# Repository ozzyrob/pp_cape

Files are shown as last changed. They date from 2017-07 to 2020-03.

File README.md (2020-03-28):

# pp_cape

Beaglebone Black cape to breakout signals to a 26 pin header

Intent is to replicate order of Parallel Port (not function)
to facilitate migration from x86 Linuxcnc users to BBB Machinekit
users

  * Port 1 header has 8 Outputs + 5 Inputs + 4 Outputs
  * Port 2 header has 8 Inputs + 5 Inputs + 4 Outputs
  * Pin 26 on each header is an "enable pin"
  * I2C is broken out to a 1x4 pin header (SCL SDL 3v3 DGND)
  * P9.1 to P9.10 are broken out to a 2x4 pin header
  * ADC Inputs and ADC ground are broken out (reference has not been)

To be used in conjunction with pp_bob_output & pp_bob_input boards

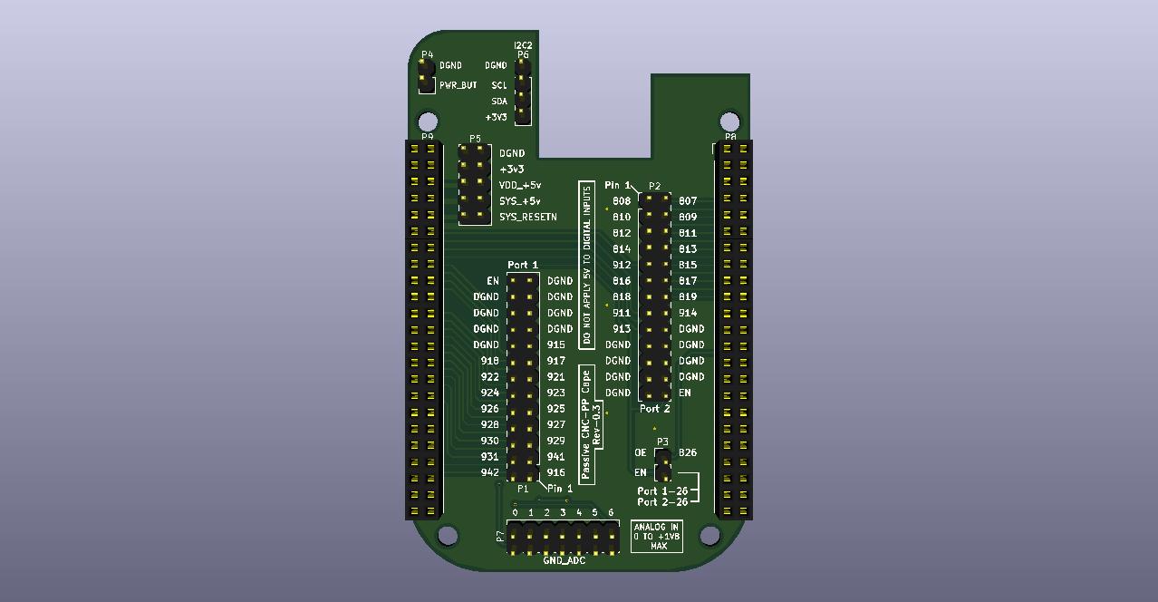
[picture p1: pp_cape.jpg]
cape


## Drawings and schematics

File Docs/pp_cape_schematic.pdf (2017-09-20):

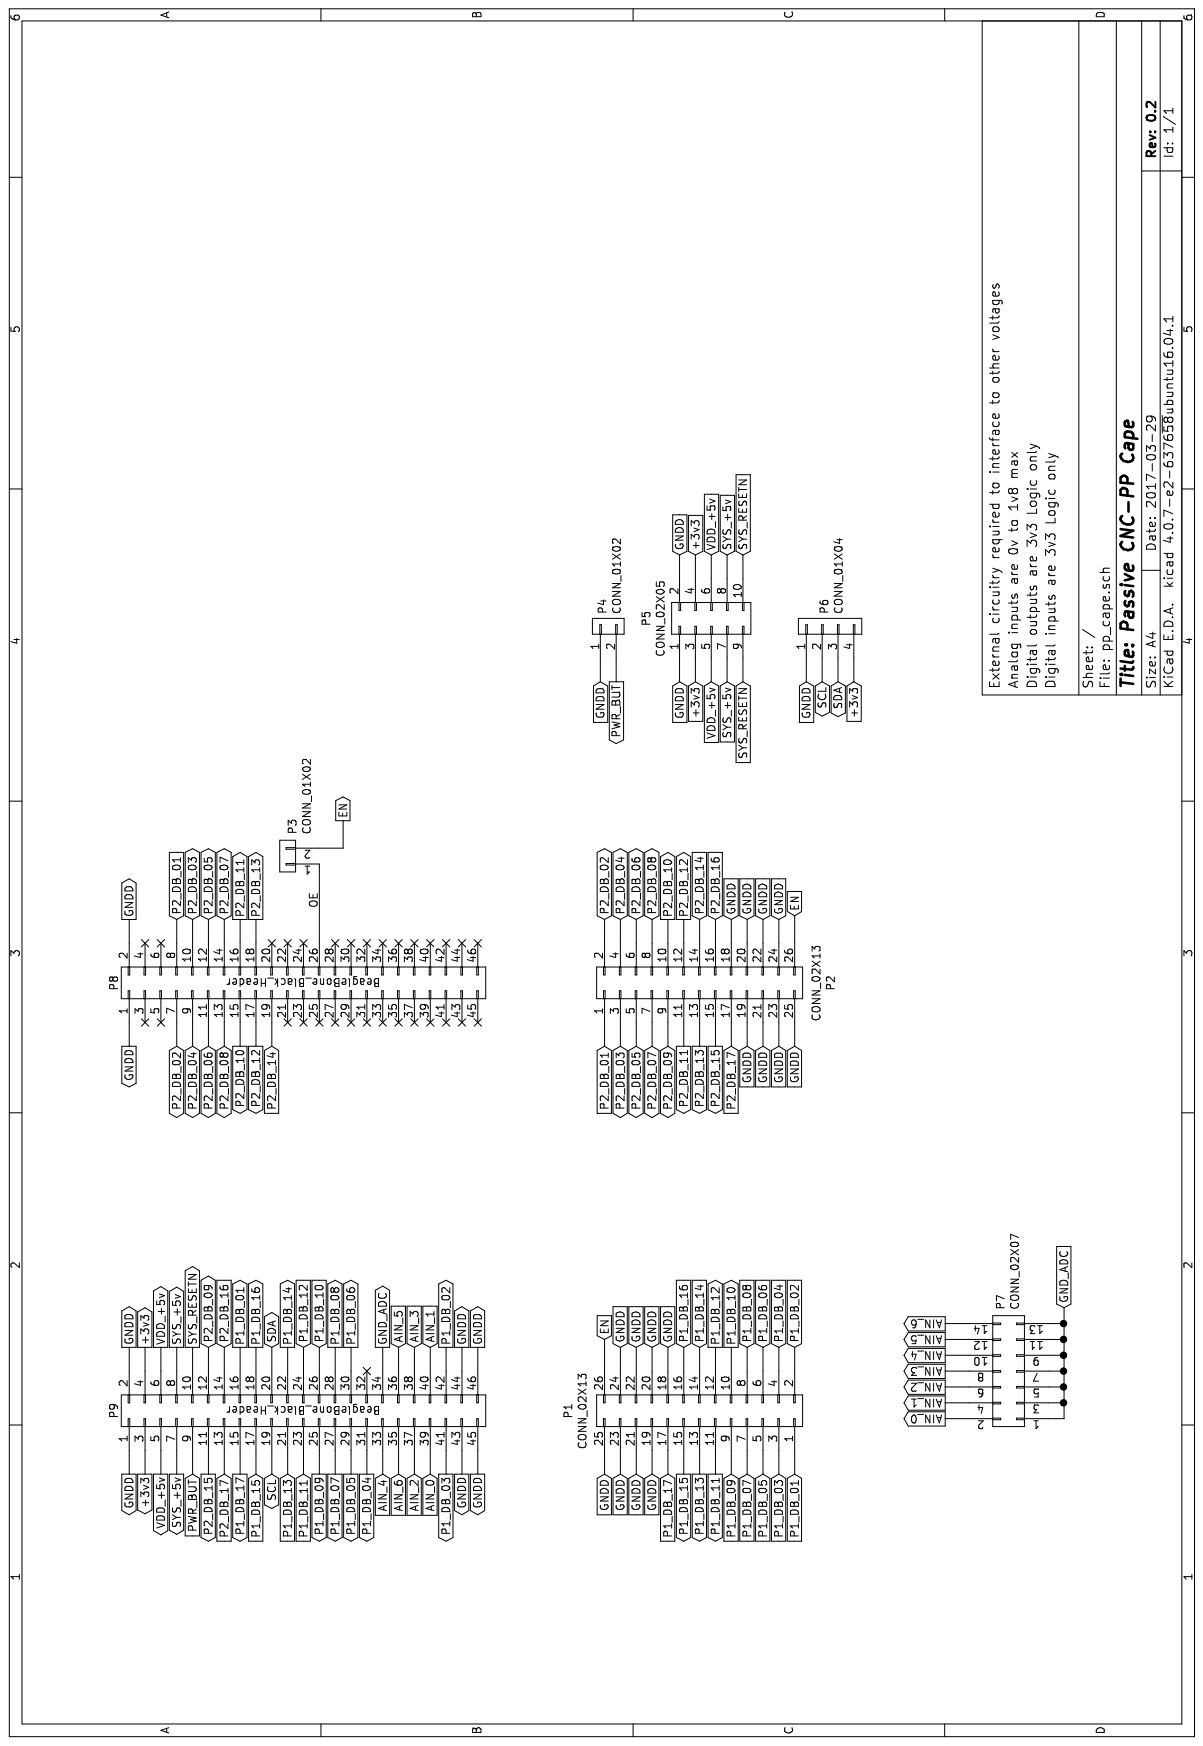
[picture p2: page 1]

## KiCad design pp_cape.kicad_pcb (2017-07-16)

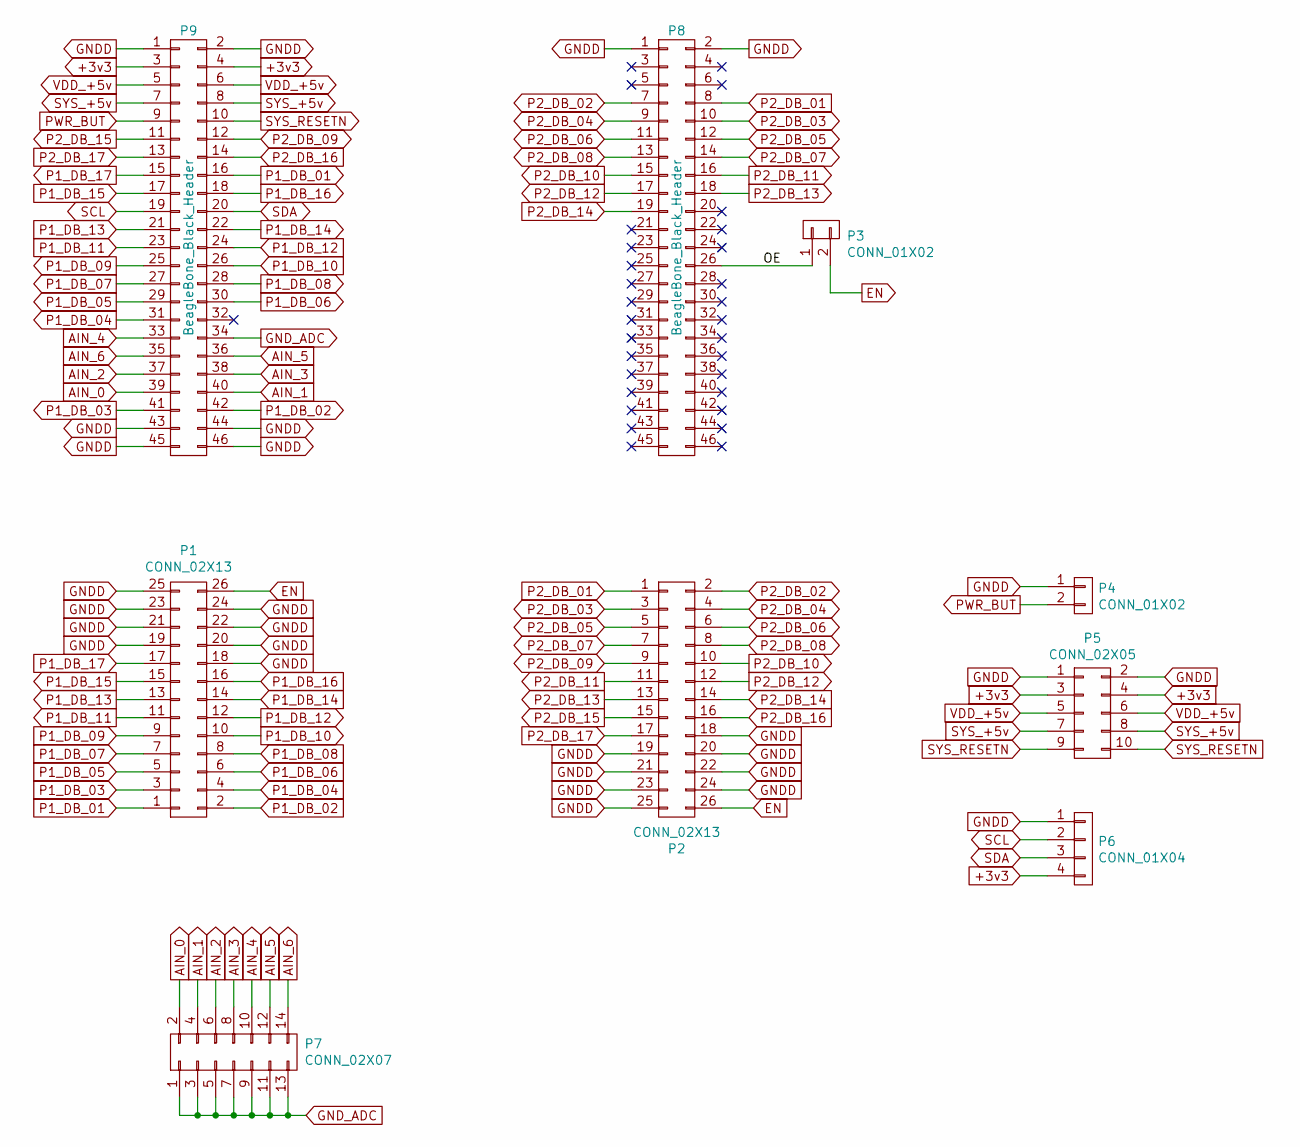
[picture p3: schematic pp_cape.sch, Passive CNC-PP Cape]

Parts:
P1, P2: CONN_02X13; Pin_Header_Straight_2x13_Pitch2.54mm
P3, P4: CONN_01X02; Pin_Header_Straight_1x02_Pitch2.54mm
P5: CONN_02X05; Pin_Header_Straight_2x05_Pitch2.54mm
P6: CONN_01X04; Pin_Header_Straight_1x04_Pitch2.54mm
P7: CONN_02X07; Pin_Header_Straight_2x07_Pitch2.54mm
P8, P9: BeagleBone_Black_Header; Socket_BeagleBone_Black

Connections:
+3v3: P5.3, P5.4, P6.4, P9.3, P9.4
/OE: P3.1, P8.26
AIN_0: P7.2, P9.39
AIN_1: P7.4, P9.40
AIN_2: P7.6, P9.37
AIN_3: P7.8, P9.38
AIN_4: P7.10, P9.33
AIN_5: P7.12, P9.36
AIN_6: P7.14, P9.35
EN: P1.26, P2.26, P3.2
GNDD: P1.18, P1.19, P1.20, P1.21, P1.22, P1.23, P1.24, P1.25, P2.18, P2.19, P2.20, P2.21, P2.22, P2.23, P2.24, P2.25, P4.1, P5.1, P5.2, P6.1, P8.1, P8.2, P9.1, P9.2, P9.43, P9.44, P9.45, P9.46
GND_ADC: P7.1, P7.3, P7.5, P7.7, P7.9, P7.11, P7.13, P9.34
P1_DB_01: P1.1, P9.16
P1_DB_02: P1.2, P9.42
P1_DB_03: P1.3, P9.41
P1_DB_04: P1.4, P9.31
P1_DB_05: P1.5, P9.29
P1_DB_06: P1.6, P9.30
P1_DB_07: P1.7, P9.27
P1_DB_08: P1.8, P9.28
P1_DB_09: P1.9, P9.25
P1_DB_10: P1.10, P9.26
P1_DB_11: P1.11, P9.23
P1_DB_12: P1.12, P9.24
P1_DB_13: P1.13, P9.21
P1_DB_14: P1.14, P9.22
P1_DB_15: P1.15, P9.17
P1_DB_16: P1.16, P9.18
P1_DB_17: P1.17, P9.15
P2_DB_01: P2.1, P8.8
P2_DB_02: P2.2, P8.7
P2_DB_03: P2.3, P8.10
P2_DB_04: P2.4, P8.9
P2_DB_05: P2.5, P8.12
P2_DB_06: P2.6, P8.11
P2_DB_07: P2.7, P8.14
P2_DB_08: P2.8, P8.13
P2_DB_09: P2.9, P9.12
P2_DB_10: P2.10, P8.15
P2_DB_11: P2.11, P8.16
P2_DB_12: P2.12, P8.17
P2_DB_13: P2.13, P8.18
P2_DB_14: P2.14, P8.19
P2_DB_15: P2.15, P9.11
P2_DB_16: P2.16, P9.14
P2_DB_17: P2.17, P9.13
PWR_BUT: P4.2, P9.9
SYS_+5v: P5.7, P5.8, P9.7, P9.8
SYS_RESETN: P5.9, P5.10, P9.10
VDD_+5v: P5.5, P5.6, P9.5, P9.6

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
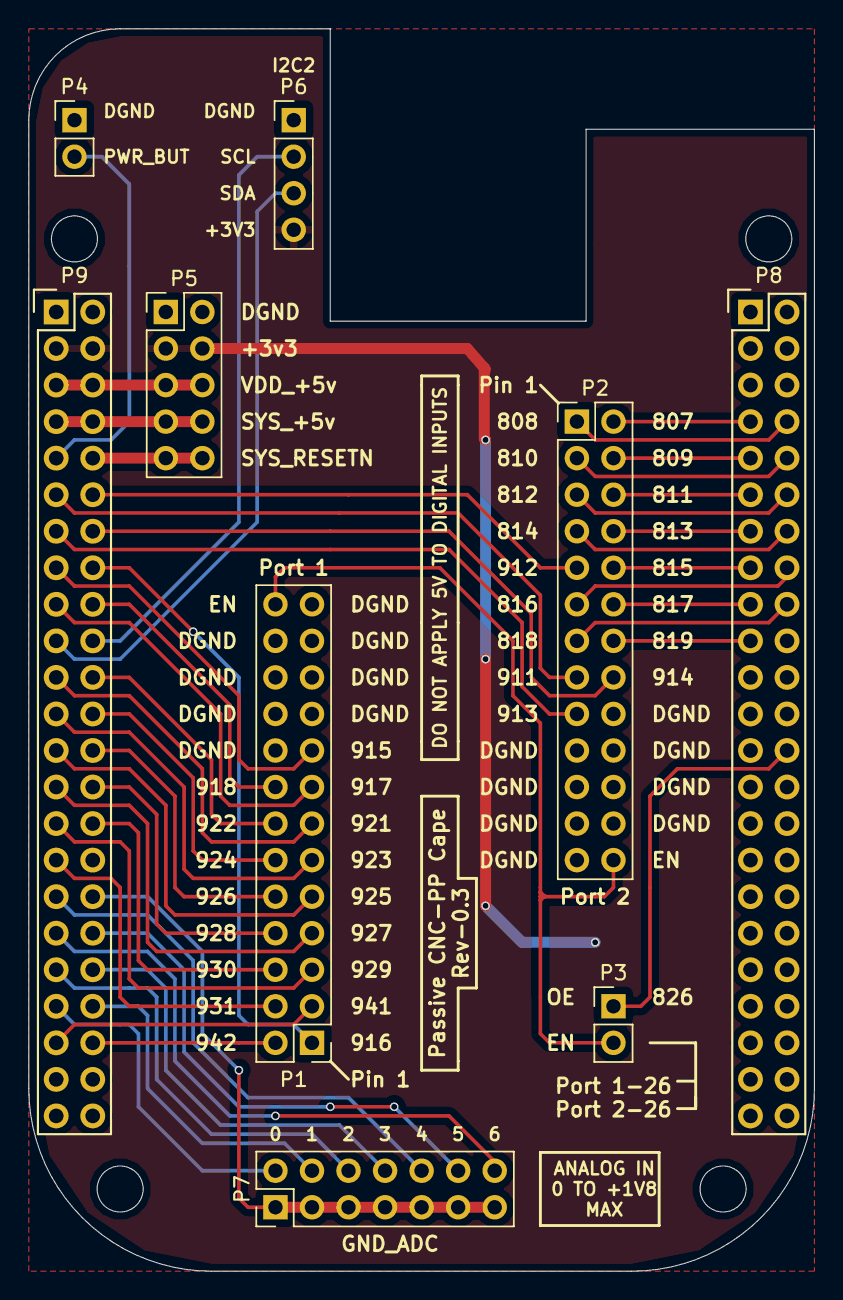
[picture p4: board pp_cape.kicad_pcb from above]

Board: 2 copper layers, 54.6 x 86.4 mm, 13 parts (0 on the bottom side), 52 nets.

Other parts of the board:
M3, M3#2: MountingHole_3.2mm_M3
mnt1, mnt2: MountingHole_3.2mm_M3

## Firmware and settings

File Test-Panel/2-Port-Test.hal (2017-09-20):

# load low-level drivers
loadusr -w ./setup.sh
loadrt hal_bb_gpio output_pins=916,942,941,931,929,930,927,928,925,922,918,915,826,808,819,913,914 input_pins=926,923,924,921,917,807,809,810,811,812,813,814,815,816,817,818,911,912
loadusr -Wn PortTest pyvcp -c PortTest 2-Port-Test.xml
loadrt threads name1=porttest period1=1000000
addf bb_gpio.read                         porttest
addf bb_gpio.write                        porttest

# BBB Enable start
# common to output & input boards
setp bb_gpio.p8.out-26.invert TRUE
net En0001 PortTest.chip-en bb_gpio.p8.out-26
# BBB Enable end

# BBB Output cape start

net db102 PortTest.btn-102 bb_gpio.p9.out-42 PortTest.led-102
net db103 PortTest.btn-103 bb_gpio.p9.out-41 PortTest.led-103
net db104 PortTest.btn-104 bb_gpio.p9.out-31 PortTest.led-104
net db105 PortTest.btn-105 bb_gpio.p9.out-29 PortTest.led-105
net db106 PortTest.btn-106 bb_gpio.p9.out-30 PortTest.led-106
net db107 PortTest.btn-107 bb_gpio.p9.out-27 PortTest.led-107
net db108 PortTest.btn-108 bb_gpio.p9.out-28 PortTest.led-108
net db109 PortTest.btn-109 bb_gpio.p9.out-25 PortTest.led-109

net db202 bb_gpio.p8.in-07 PortTest.led-202
net db203 bb_gpio.p8.in-10 PortTest.led-203
net db204 bb_gpio.p8.in-09 PortTest.led-204
net db205 bb_gpio.p8.in-12 PortTest.led-205
net db206 bb_gpio.p8.in-11 PortTest.led-206
net db207 bb_gpio.p8.in-14 PortTest.led-207
net db208 bb_gpio.p8.in-13 PortTest.led-208
net db209 bb_gpio.p9.in-12 PortTest.led-209


net db110 bb_gpio.p9.in-26 PortTest.led-110
net db111 bb_gpio.p9.in-23 PortTest.led-111
net db112 bb_gpio.p9.in-24 PortTest.led-112
net db113 bb_gpio.p9.in-21 PortTest.led-113
net db115 bb_gpio.p9.in-17 PortTest.led-115

net db210 bb_gpio.p8.in-15 PortTest.led-210
net db211 bb_gpio.p8.in-16 PortTest.led-211
net db212 bb_gpio.p8.in-17 PortTest.led-212
net db213 bb_gpio.p8.in-18 PortTest.led-213
net db215 bb_gpio.p9.in-11 PortTest.led-215

net db101 PortTest.btn-101 bb_gpio.p9.out-16 PortTest.led-101
net db114 PortTest.btn-114 bb_gpio.p9.out-22 PortTest.led-114
net db116 PortTest.btn-116 bb_gpio.p9.out-18 PortTest.led-116
net db117 PortTest.btn-117 bb_gpio.p9.out-15 PortTest.led-117

net db201 PortTest.btn-201 bb_gpio.p8.out-08 PortTest.led-201
net db214 PortTest.btn-214 bb_gpio.p8.out-19 PortTest.led-214
net db216 PortTest.btn-216 bb_gpio.p9.out-13 PortTest.led-216
net db217 PortTest.btn-217 bb_gpio.p9.out-14 PortTest.led-217

# BBB Ouput Cape end



start

# loadusr halmeter

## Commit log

2017-04-19 Initial commit warning ethernet cut out incorrect
    [pp_cape_v02.kicad_pcb, pp_cape_v02.sch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]
2017-04-19 Version V0.3 fixed ethernt cut out amended silkscreen adjusted I2C2 tracks
    [pp_cape.kicad_pcb, pp_cape.sch]
2017-04-19 Remove *_V02 files
    [pp_cape_v02.kicad_pcb, pp_cape_v02.sch]
2017-04-19 Renamed files deleting V02 part
    [pp_cape.kicad_pcb, pp_cape.sch]
2017-07-16 drop -v0.2 from footprints
2017-07-16 Added board picture and edited Master.txt
2017-07-16 Added V0.2 suffix to manufacture directory to match board verison that was manufactured
    [pp_cape_v02.GBL, pp_cape_v02.GBO, pp_cape_v02.GBS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]
2017-07-16 Cleaned up sign off
    [pp_cape.kicad_pcb, pp_cape.sch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]
2017-09-15 Upload New File
    [Pin Assignments.ods]
2017-09-20 Update 2-Port-Test.hal
    Chnage from 2xx to 9xx numbering
    [2-Port-Test.hal]
2017-09-20 Add spreadsheet showing pin assignments
    [Pin-Assignments.ods]
2017-09-20 Deleted pin assignment spreadsheet form Dcos
    [Pin-Assignments.ods]
